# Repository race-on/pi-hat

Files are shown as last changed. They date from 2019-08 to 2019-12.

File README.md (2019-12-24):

Race On Pi HAT
=====

A Raspberry Pi HAT to control a self-driving car. HAT includes:
1. 3.5A DC-DC converter to power the Pi from a battery (2-3 LiPo cells)
2. 10A H-bridge for DC motor control
3. 3A LDO to power servo at 6V for faster response time
4. Battery alarm when the voltage drops under 6V
5. I2C accelerometer interface
6. Interface for encoders based on the QRE1113 analog line sensor
7. Compatible with Jetson Nano
8. Reverse polarity protection
9. Optimized for Seeed Studio PCBA

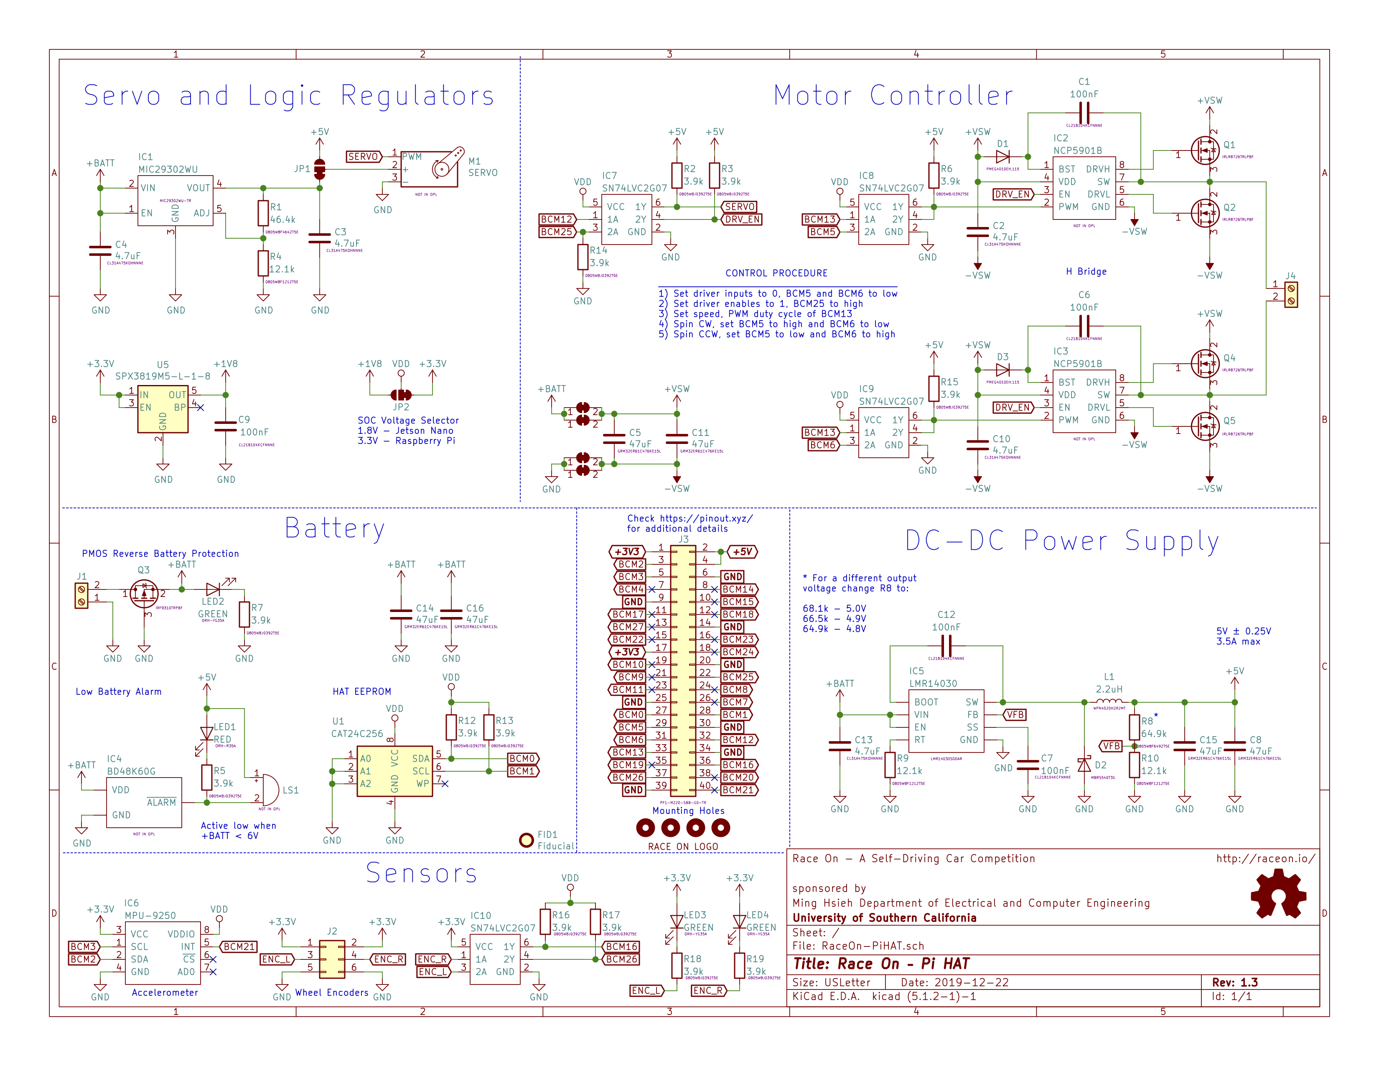
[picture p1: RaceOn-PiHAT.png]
Pi HAT Schematic


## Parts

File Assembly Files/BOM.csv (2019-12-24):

Designator | Manufacturer Part Number or Seeed SKU | Qty
C1, C6, C7, C9, C12 | CL21B104KCFNNNE | 5
C2, C3, C4, C10, C13 | CL31A475KOHNNNE | 5
C5, C8, C11, C14, C15, C16 | CL32A226KAJNNNE | 6
D1, D3 | PMEG4010EH,115 | 2
D2 | MBRS540T3G | 1
IC1 | SPX29302T5-L/TR | 1
IC5 | LMR14030SDDAR | 1
IC7, IC8, IC9, IC10 | SN74LVC2G07DBVR | 4
J2 | A2541WV-2x3P | 1
J3 | PF1-M220-SBB-G0-TR | 1
J1, J4 | 1935161 | 2
L1 | WPN4020H2R2MT | 1
LED1 | ORH-R35A | 1
LED2, LED3, LED4 | ORH-YG35A | 3
M1 | A2543WV-3P | 1
Q3 | IRF9310TRPBF | 1
Q1, Q2, Q4, Q5 | IRLR8726TRLPBF | 4
R1 | 0805W8F4642T5E | 1
R2, R3, R5, R6, R7, R12, R13, R14, R15, R16, R17, R18, R19 | 0805W8J0392T5E | 13
R8 | 0805W8F6492T5E | 1
R4, R9, R10 | 0805W8F1212T5E | 3
U1 | CAT24C256WI-GT3 | 1
U5 | SPX3819M5-L-1-8/TR | 1

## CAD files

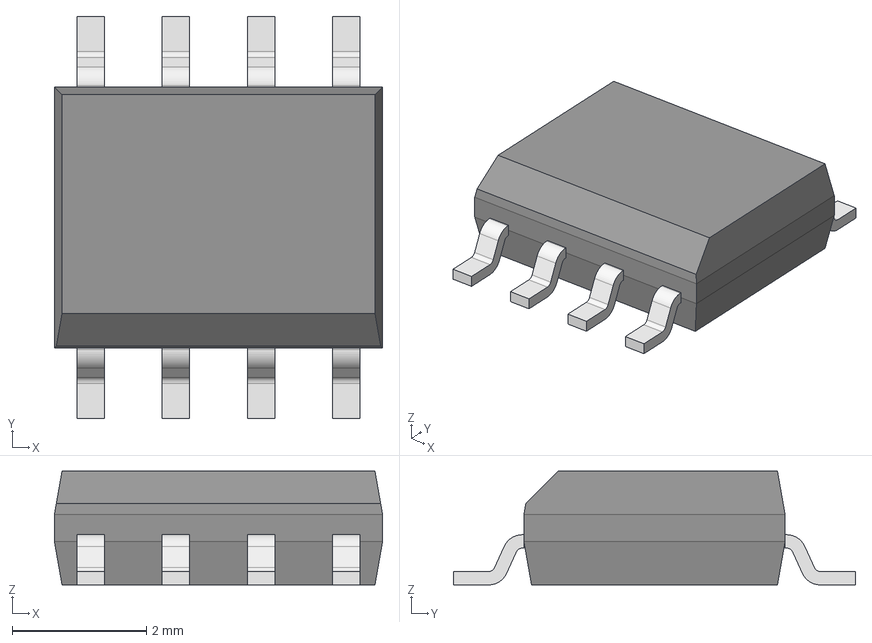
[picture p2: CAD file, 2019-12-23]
3D Models/SOIC9P127_490X600X170L83X41T287X202.STEP
4.90 x 6.00 x 1.70 mm

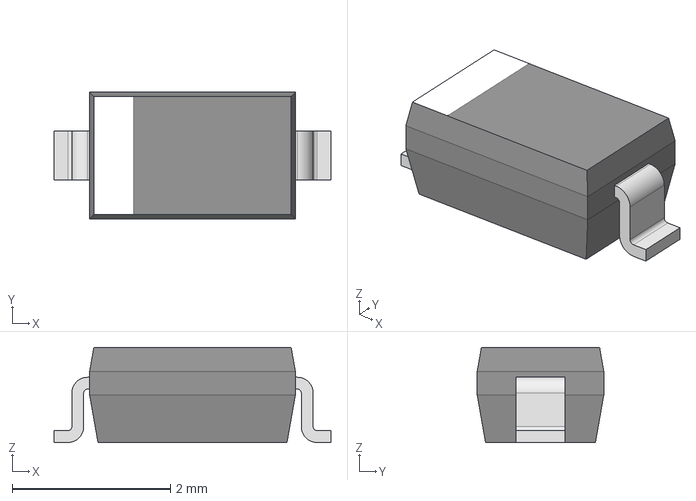
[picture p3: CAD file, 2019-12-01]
3D Models/SOD350X160X120L45X62.STEP
3.50 x 1.60 x 1.20 mm

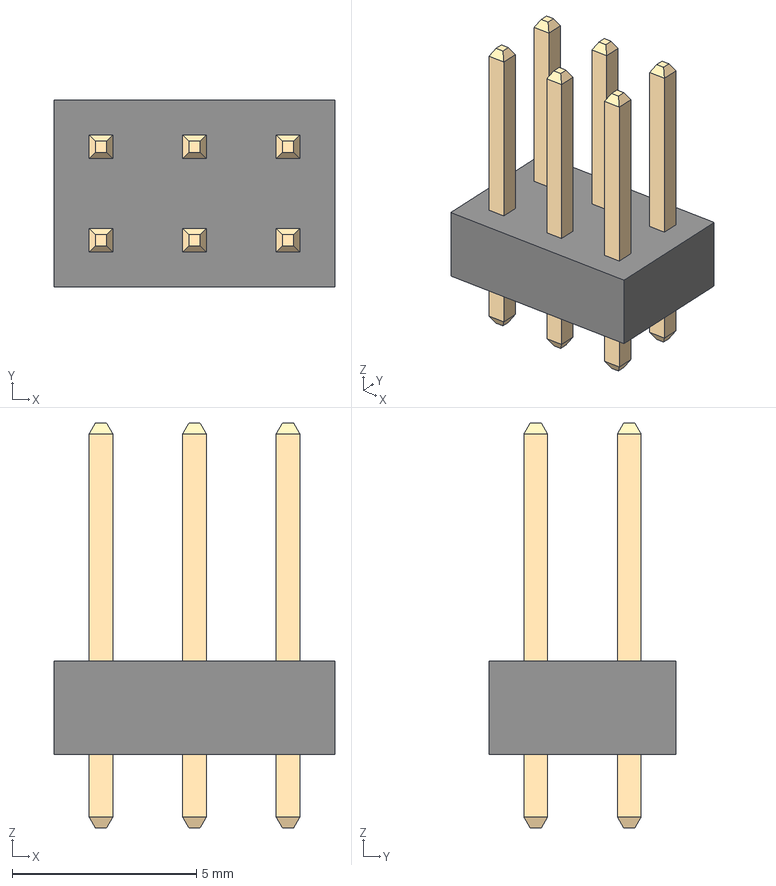
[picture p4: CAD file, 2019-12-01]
3D Models/HDRV6W65P254_3X2_762X508H900.STEP
7.62 x 5.08 x 11.0 mm

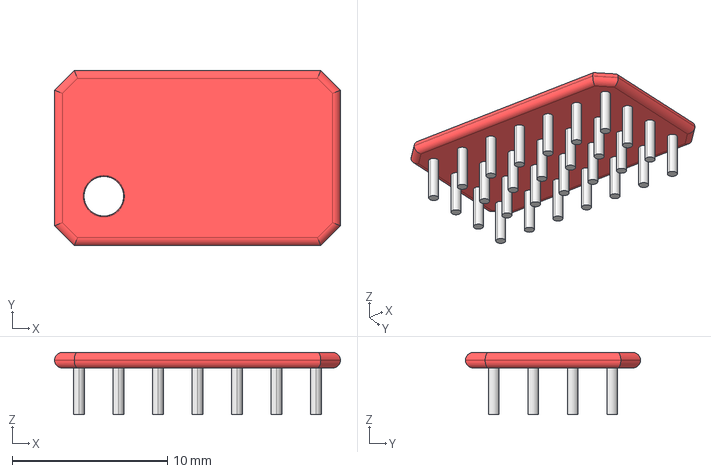
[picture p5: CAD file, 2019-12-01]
3D Models/PGA28P254C7R4L1840X1127H200.STEP
18.4 x 11.3 x 4.00 mm

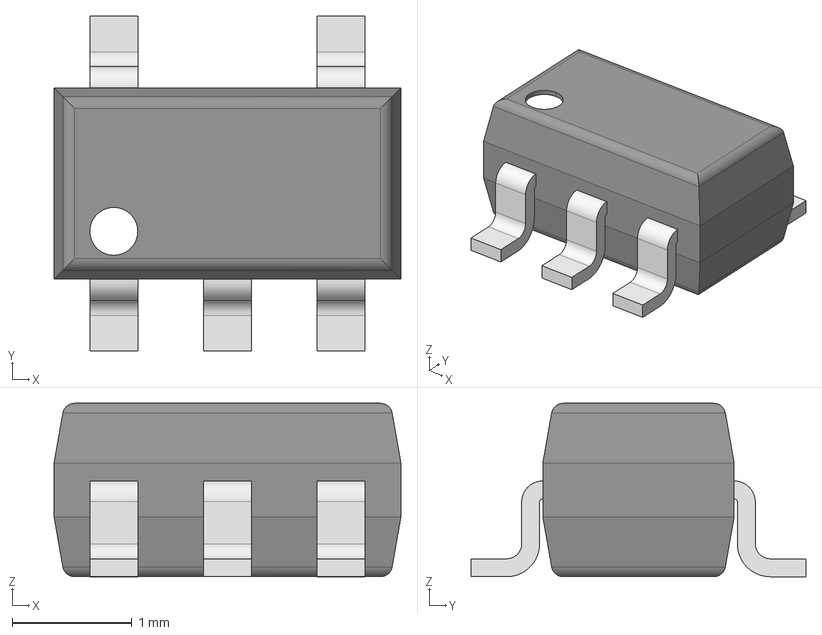
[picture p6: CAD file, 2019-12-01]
3D Models/SOT23-5P95_280X145L45X40.STEP
2.90 x 2.80 x 1.45 mm

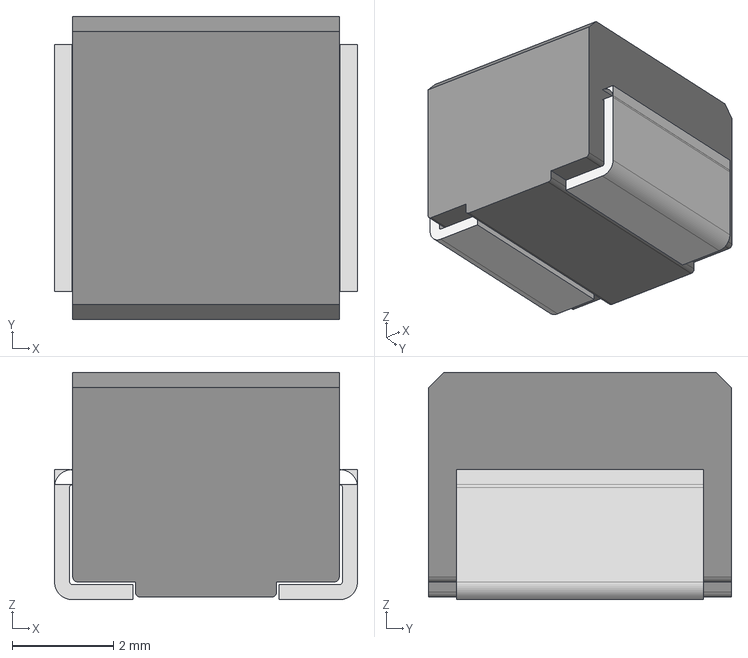
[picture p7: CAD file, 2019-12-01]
3D Models/INDM600X600X450L155X490.STEP
6.00 x 6.00 x 4.50 mm

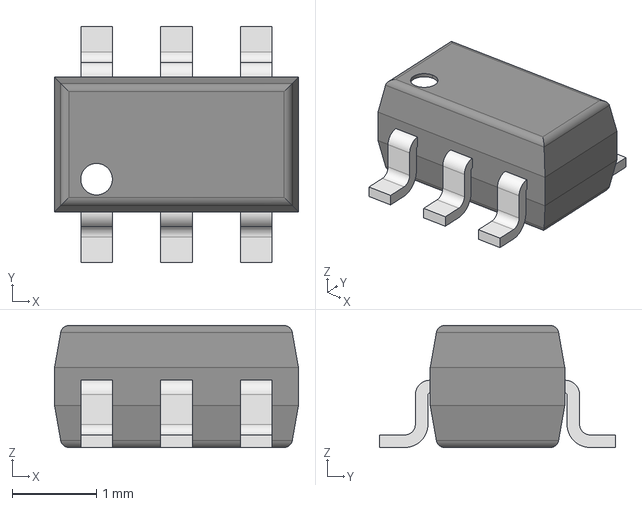
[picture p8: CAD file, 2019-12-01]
3D Models/SOT23-6P95_280X145L45X37.STEP
2.90 x 2.80 x 1.45 mm

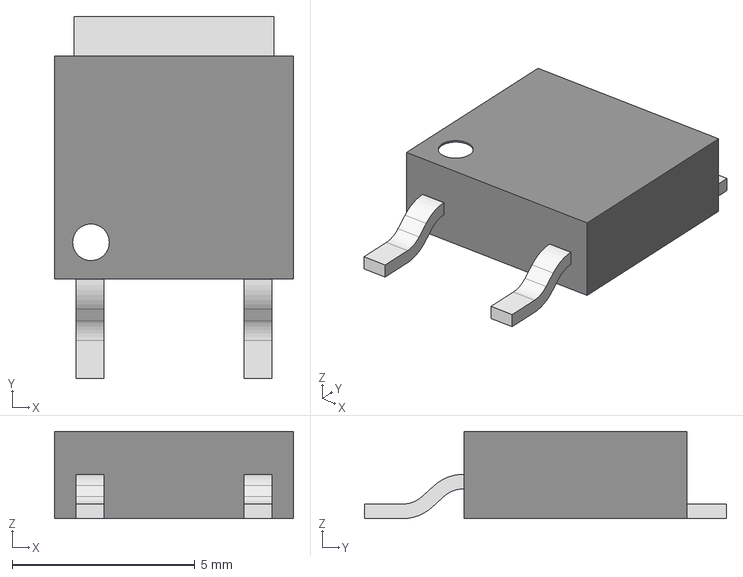
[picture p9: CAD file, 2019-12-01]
3D Models/DPAK3P460_990X239L160X76T650X546.STEP
6.54 x 9.90 x 2.39 mm

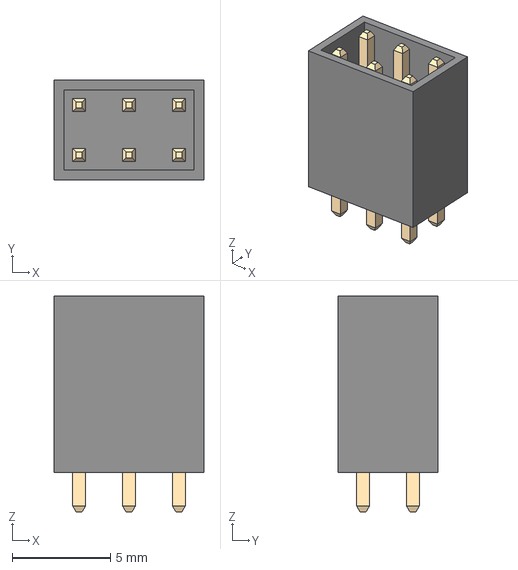
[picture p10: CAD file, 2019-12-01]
3D Models/SHDRV6W65P254_3X2_762X508H900.STEP
7.62 x 5.08 x 11.0 mm

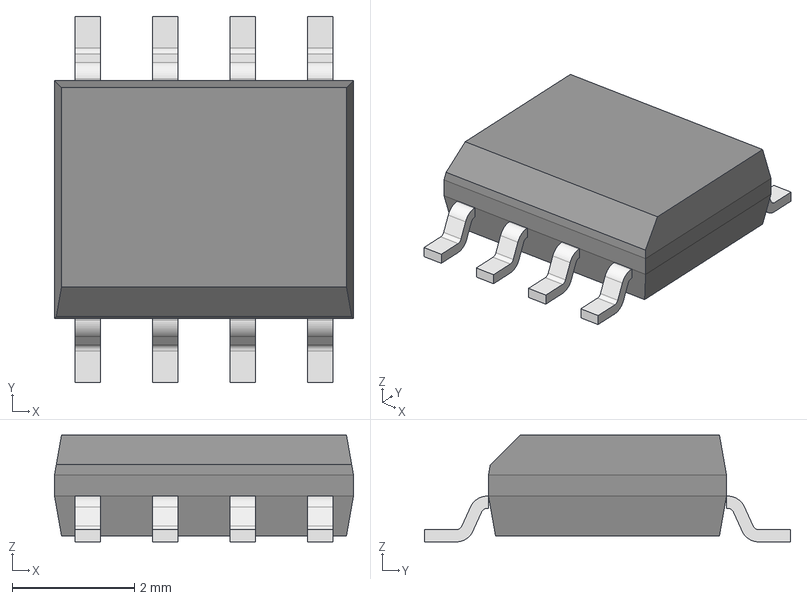
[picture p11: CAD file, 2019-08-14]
3D Models/SOIC8P127_490X600X175L83X42.STEP
4.90 x 6.00 x 1.75 mm

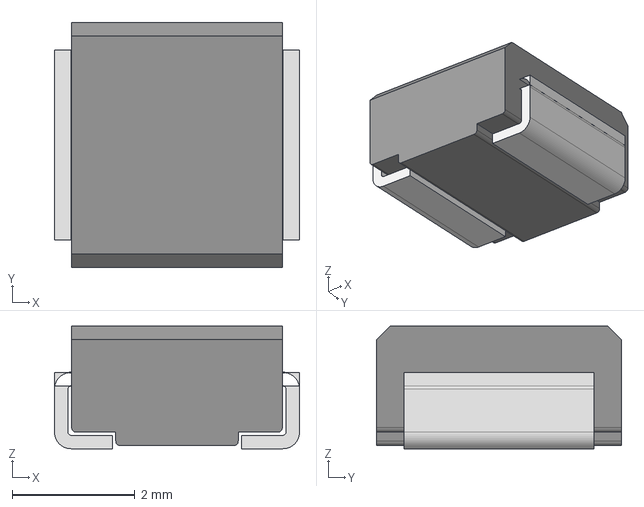
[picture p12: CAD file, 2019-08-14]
3D Models/INDM400X400X200L95X310.STEP
4.00 x 4.00 x 2.00 mm

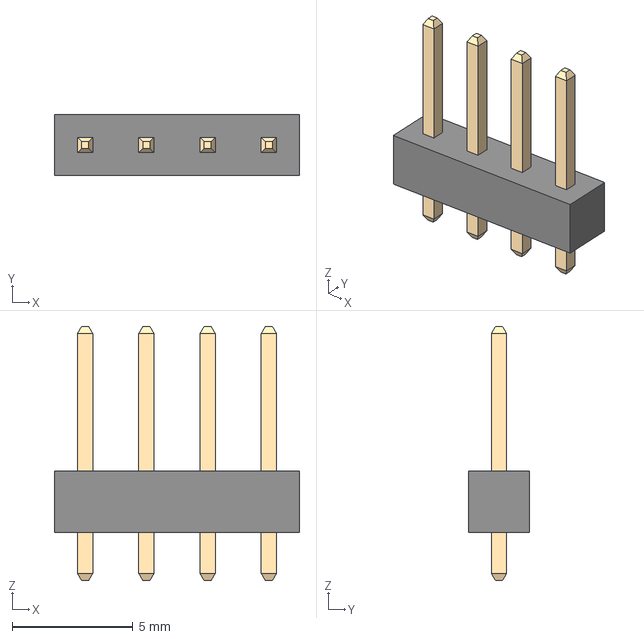
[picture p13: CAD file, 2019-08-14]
3D Models/HDRV4W64P254_4X1_1016X254H854.STEP
10.2 x 2.54 x 10.5 mm

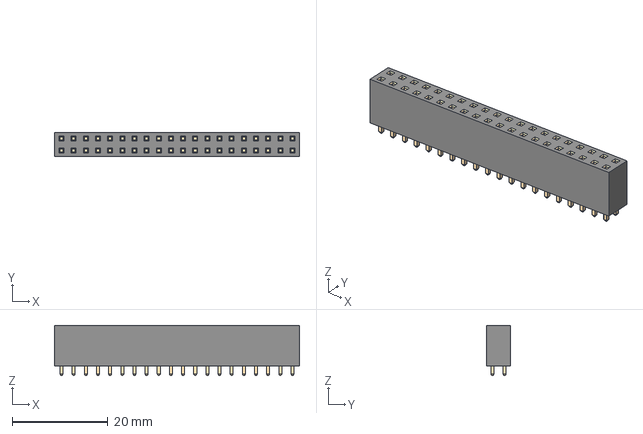
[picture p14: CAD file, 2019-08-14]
3D Models/RHDRV40W64P254_20X2_5120X500H850.STEP
51.2 x 5.00 x 10.5 mm

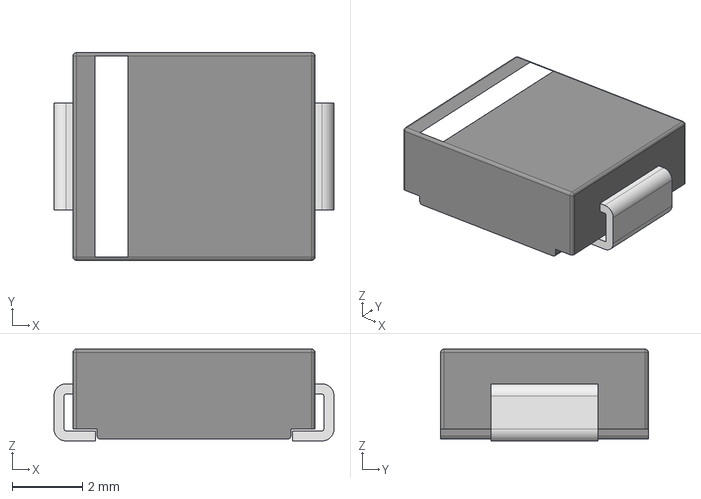
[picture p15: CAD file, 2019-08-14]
3D Models/DIOM795X590X261L117X305.STEP
7.95 x 5.90 x 2.61 mm

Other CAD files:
3D Models/CAPPM730X435X310L135X240.STEP
3D Models/CAPC320X160X180L50.STEP
3D Models/ICSOFL8P127_515X615X112L61X42.STEP
3D Models/CAPC320X250X270L60.STEP
3D Models/BTN4P450_600X900X350L83X70M.STEP
3D Models/CAPC200X125X95L45.STEP
3D Models/DPAK6P67_587X190L89X29T300X275.STEP
3D Models/HDRV3W64P254_3X1_762X254H854.STEP
3D Models/LEDC197X125X85L45.STEP
3D Models/LSP500W60D980H500.STEP
3D Models/RESC200X127X65L40.STEP
3D Models/SOT23-3P95_280X125L45X40.STEP

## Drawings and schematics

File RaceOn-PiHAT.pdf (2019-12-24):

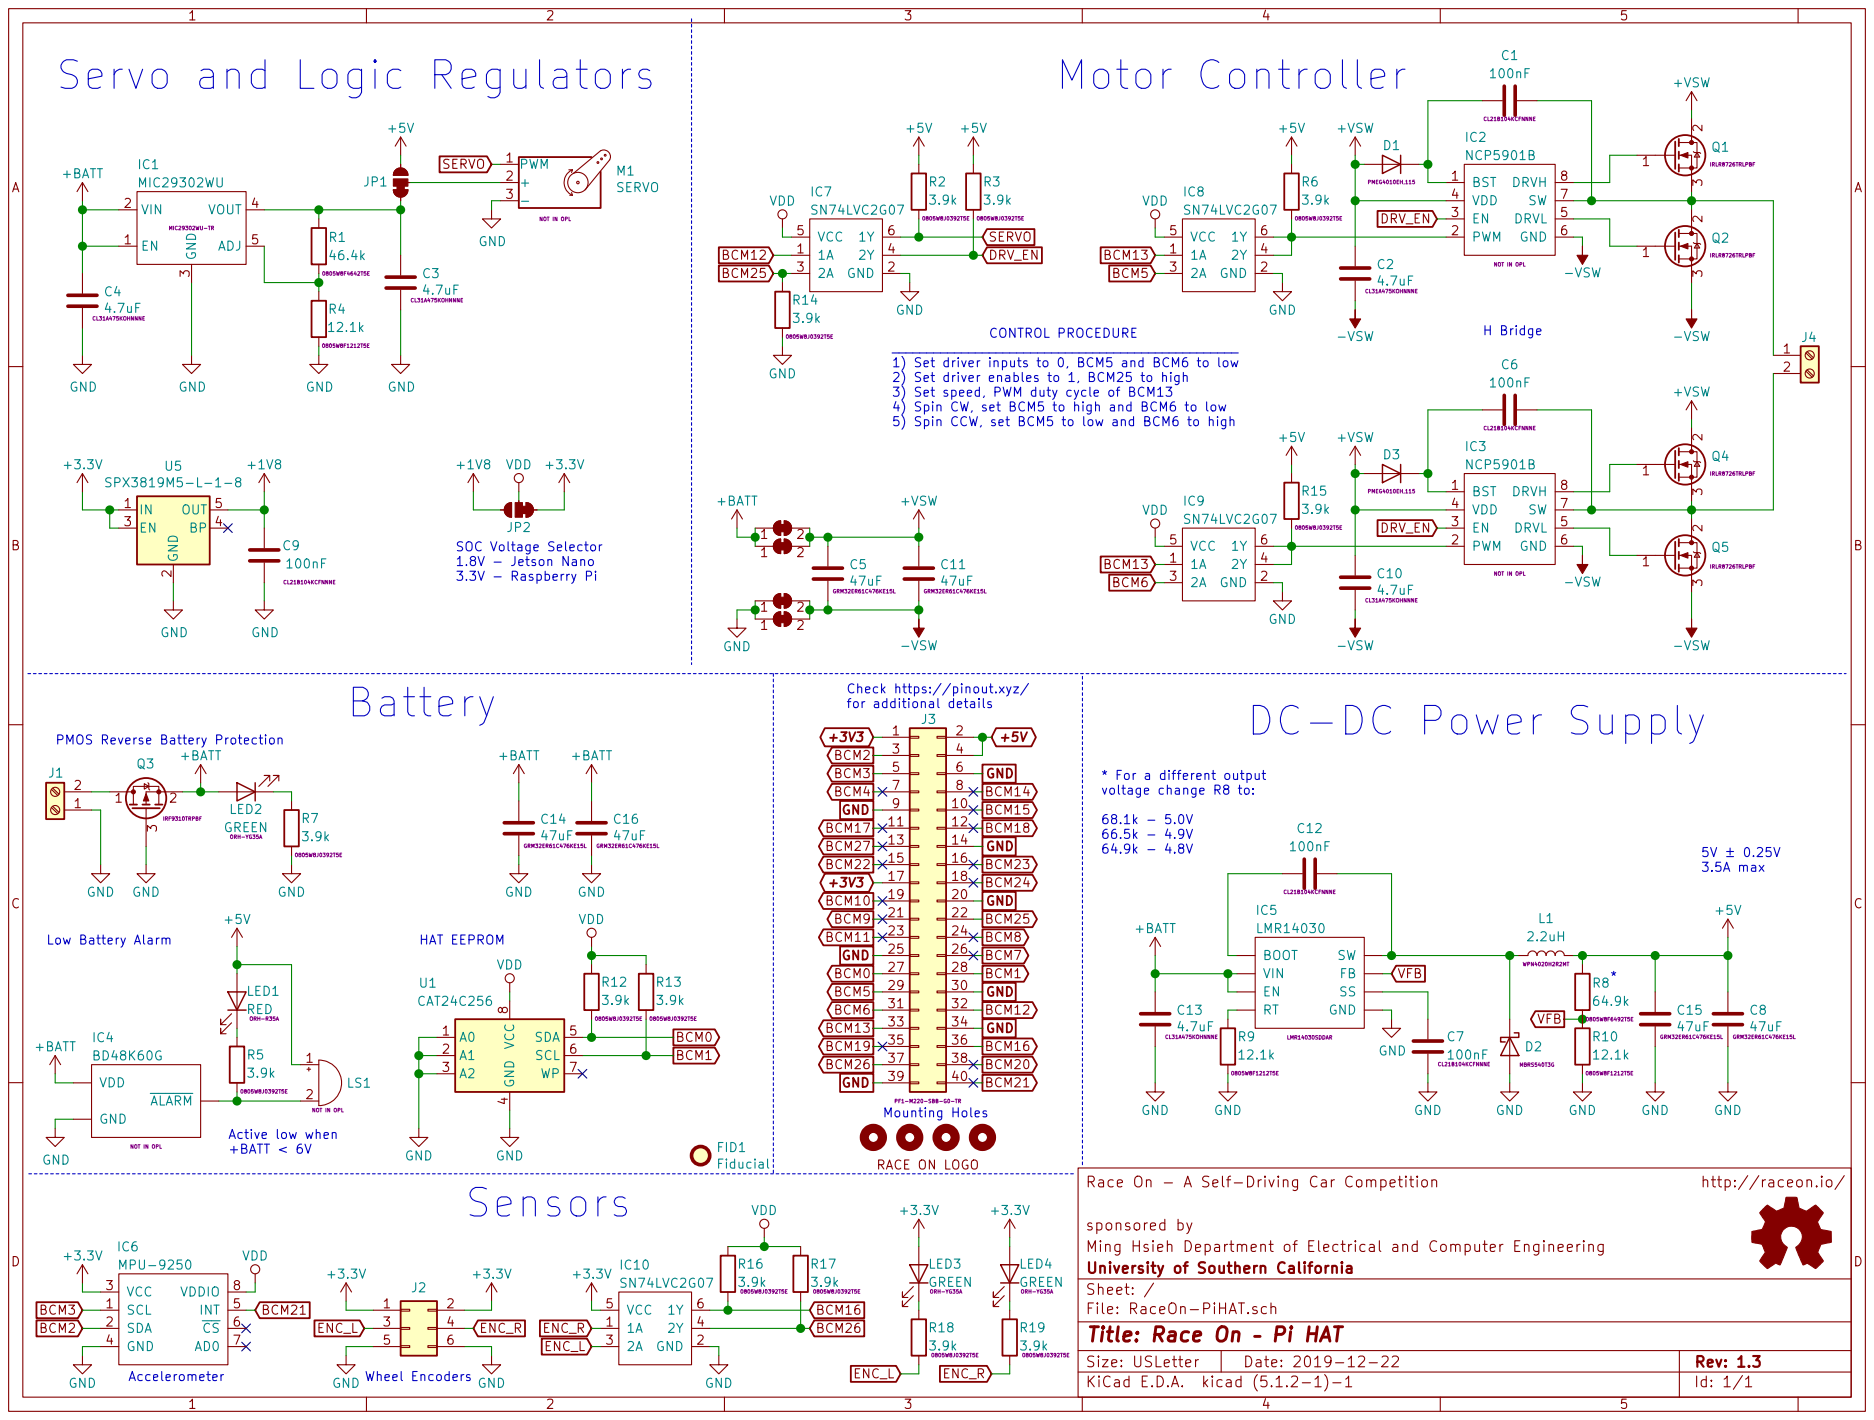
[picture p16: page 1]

+5V Servo and Logic Regulators

1) Set driver inputs to 0, BCM5 and BCM6 to low
2) Set driver enables to 1, BCM25 to high
3) Set speed, PWM duty cycle of BCM13
4) Spin CW, set BCM5 to high and BCM6 to low
5) Spin CCW, set BCM5 to low and BCM6 to high

SOC Voltage Selector 1.8V - Jetson Nano

+3V3 Check https://pinout.xyz/

VFB DC-DC Power Supply

4 SDA 5 SCL 6 WP 7 VCC

Active low when +BATT < 6V

sponsored by
Ming Hsieh Department of Electrical and Computer Engineering
File: RaceOn-PiHAT.sch Sheet: / University of Southern California

Id: 1/1 Title: Race On Pi HAT

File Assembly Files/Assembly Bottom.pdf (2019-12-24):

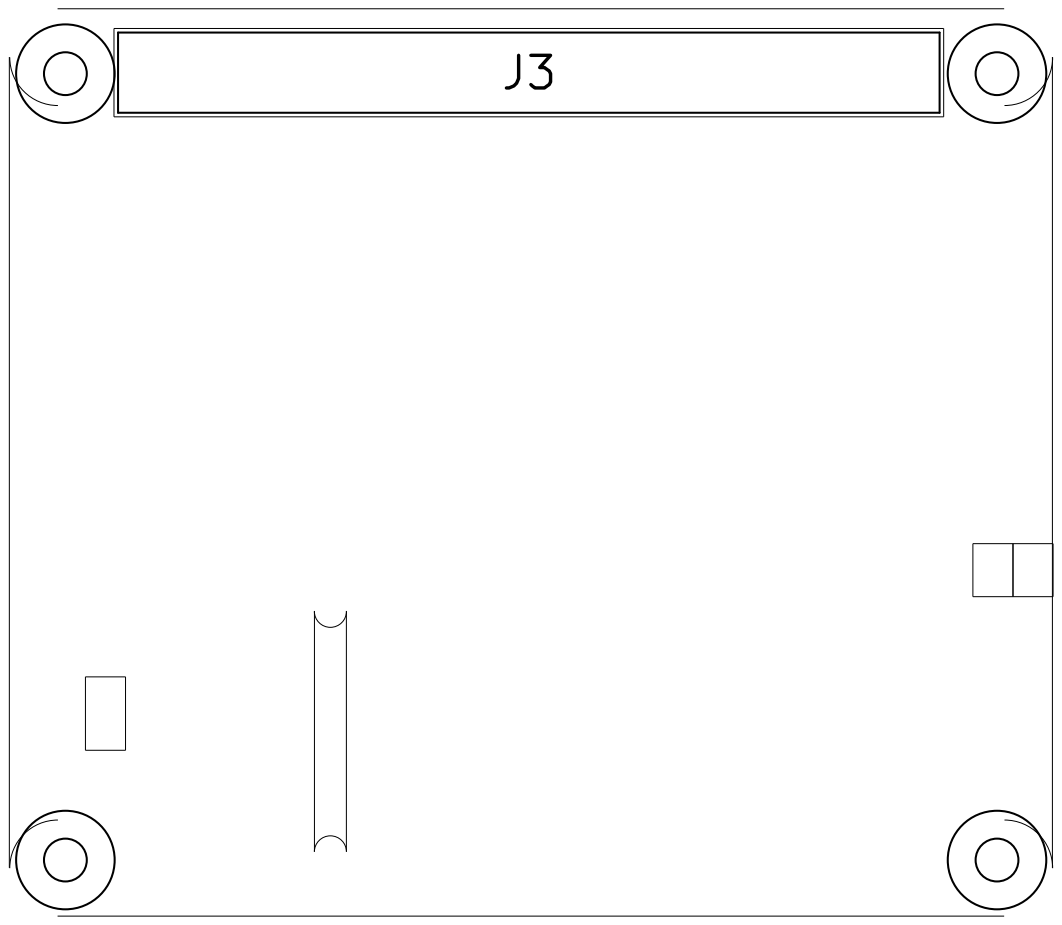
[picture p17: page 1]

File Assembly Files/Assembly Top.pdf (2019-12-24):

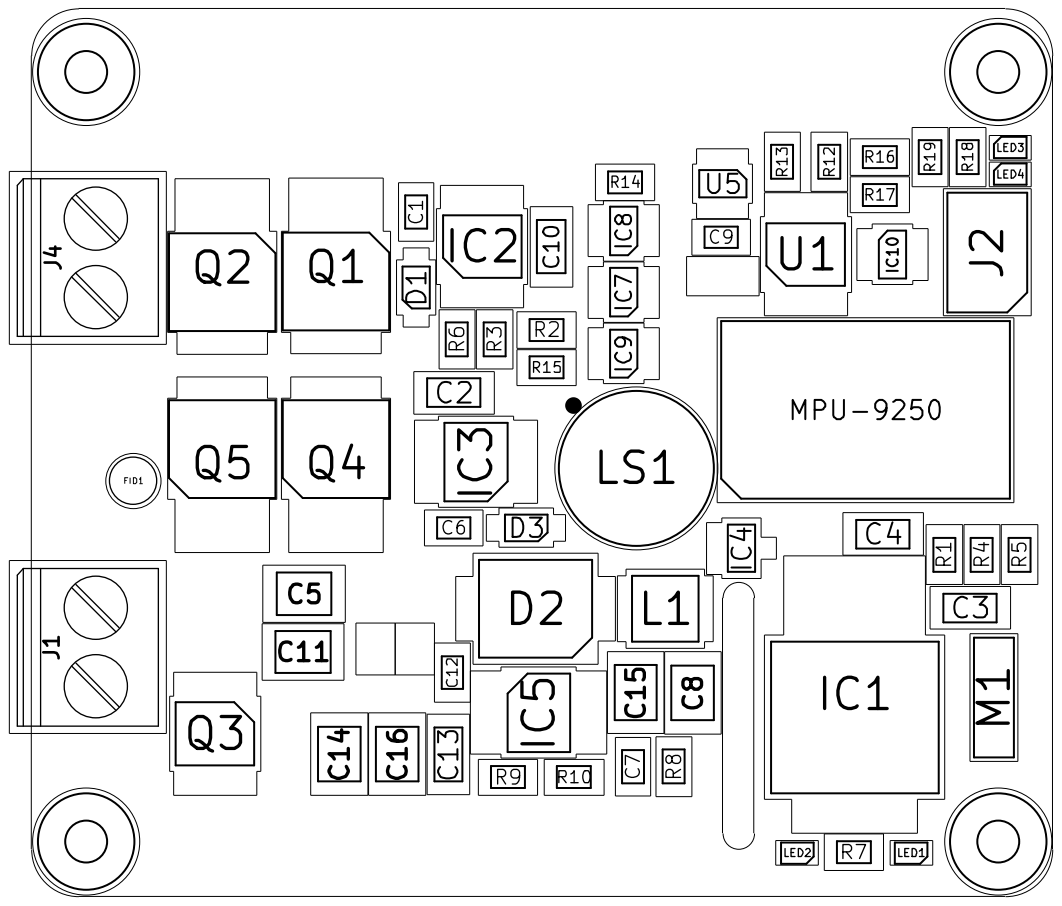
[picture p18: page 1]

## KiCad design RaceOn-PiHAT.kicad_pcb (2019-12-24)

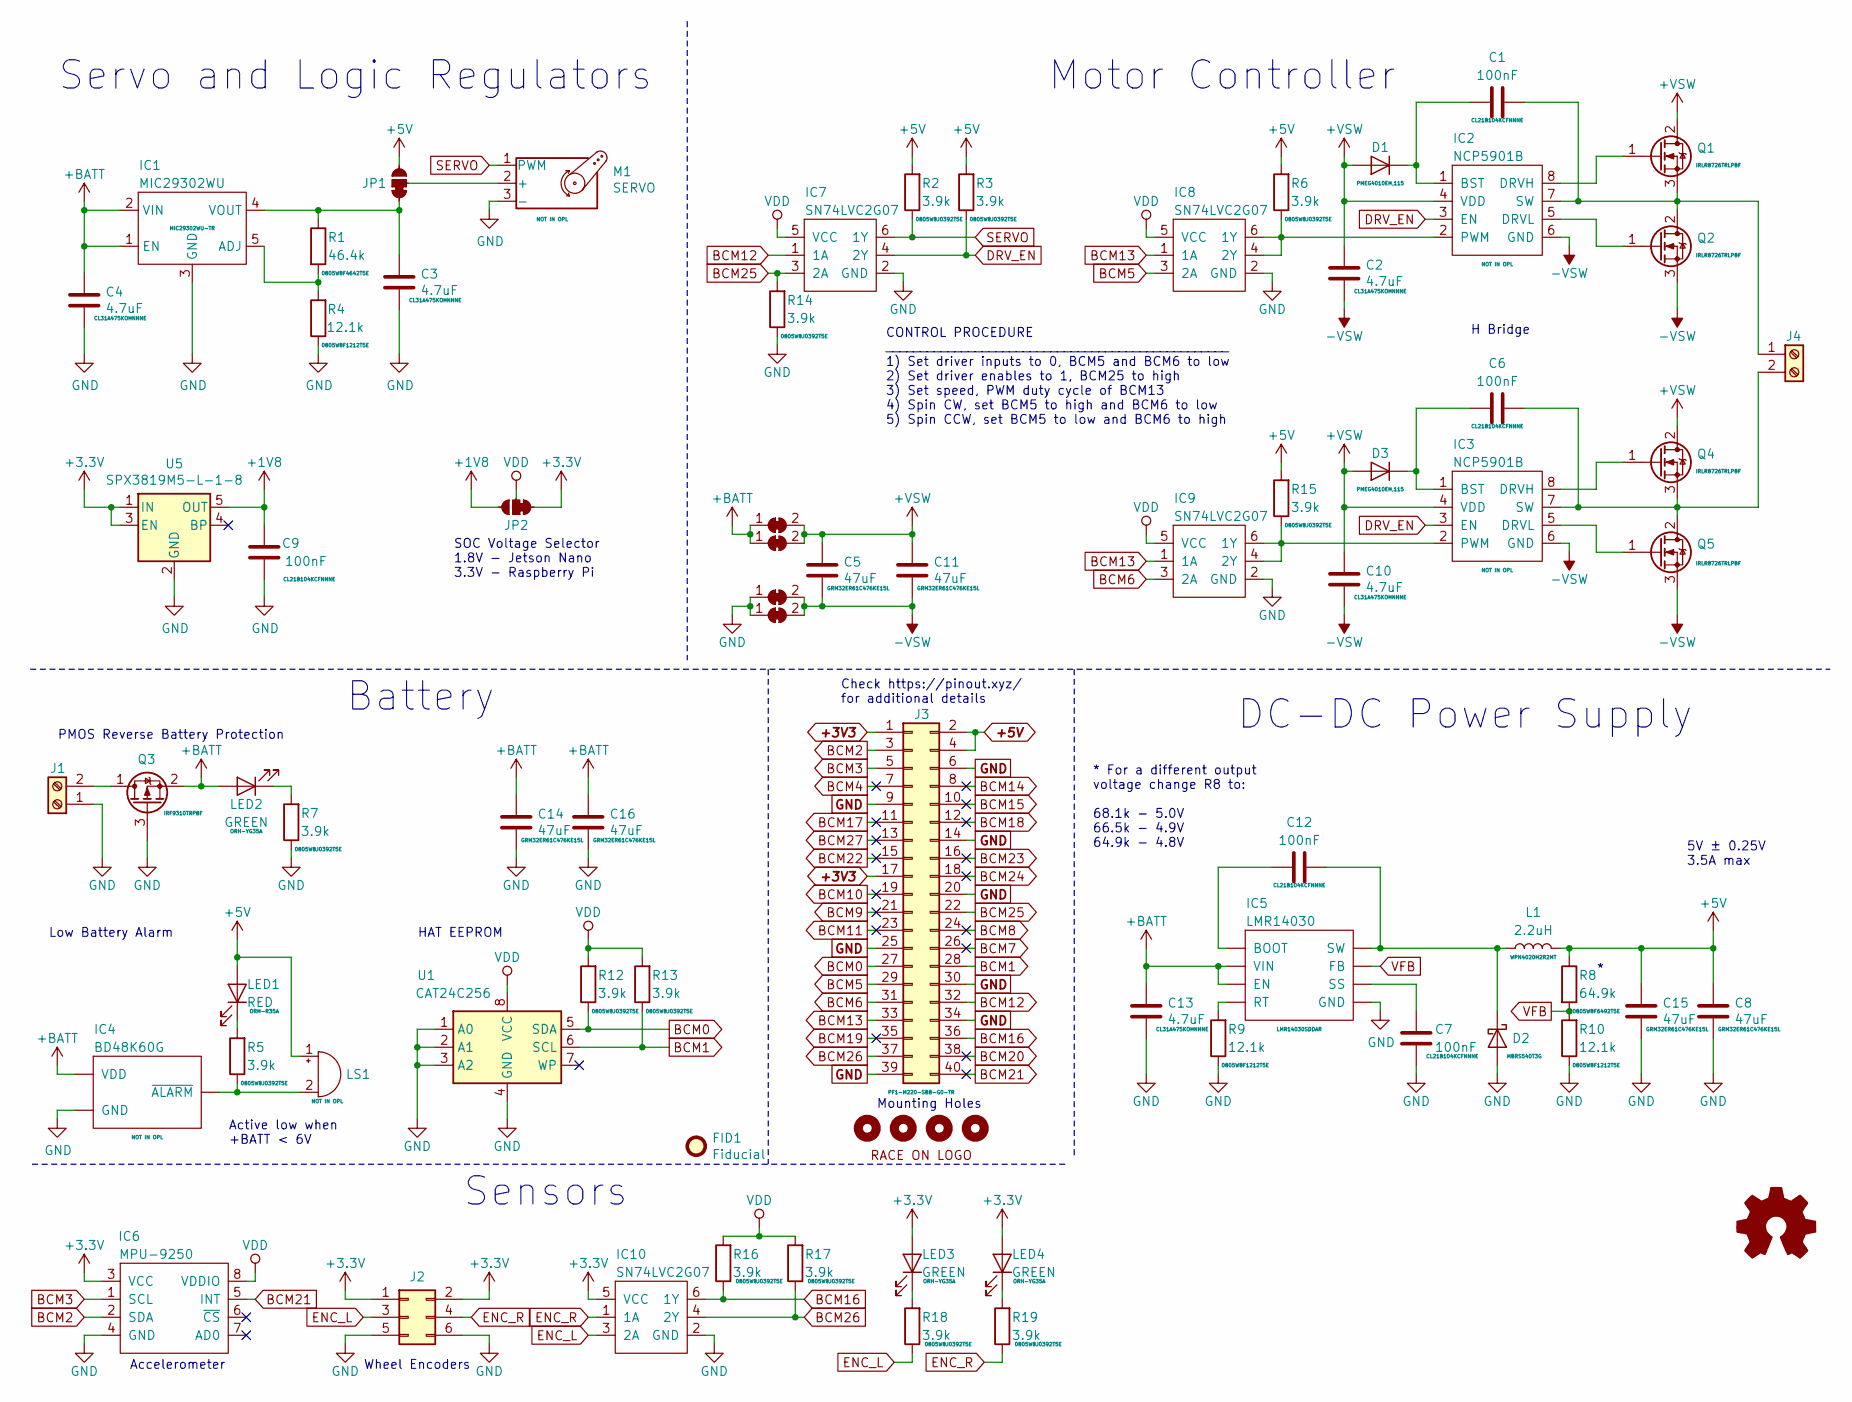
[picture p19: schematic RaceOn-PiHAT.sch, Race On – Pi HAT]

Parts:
C1, C6, C7, C9, C12: 100nF; CAPC200X125X95L45M; MPN CL21B104KCFNNNE
C2, C3, C4, C10, C13: 4.7uF; CAPC320X160X180L50M; MPN CL31A475KOHNNNE
C5, C8, C11, C14, C15, C16: 47uF; CAPC320X250X270L60M; MPN GRM32ER61C476KE15L
D1, D3: D; SOD350X160X120L45X62M; MPN PMEG4010EH,115
D2: D_Schottky; DIOM795X590X261L117X305M; MPN MBRS540T3G
FID1: Fiducial; FID1M3
H1, H2, H3, H4: MountingHole; MTGP620H275V8H50
IC1: MIC29302WU; DPAK6P67_587X190L89X29T300X275M; MPN MIC29302WU-TR
IC2, IC3: NCP5901B; SOIC8P127_490X600X175L83X42M; MPN NOT IN OPL
IC4: BD48K60G; SOT23-3P95_280X125L45X40M; MPN NOT IN OPL
IC5: LMR14030; SOIC9P127_490X600X170L83X41T287X202; MPN LMR14030SDDAR
IC6: MPU-9250; PGA28P254C7R4L1840X1127H200
IC7, IC8, IC9, IC10: SN74LVC2G07; SOT23-6P95_280X145L45X37M; MPN SN74LVC2G07DBVR
J1, J4: Screw_Terminal_01x02; TerminalBlock_Phoenix_PT-1,5-2-5.0-H_1x02_P5.00mm_Horizontal; MPN 1935161
J2: Conn_02x03_Odd_Even; HDRV6W65P254_3X2_762X508H900; MPN A2541WV-2x3P
J3: Pi Connector; RHDRV40W64P254_20X2_5120X500H850; MPN PF1-M220-SBB-G0-TR
JP1, JP2: SolderJumper; SJ3B12P10X15
JP3, JP4, JP5, JP6: SolderJumper_2_Bridged; SolderJumper-2_P1.3mm_Bridged_Pad1.0x1.5mm
L1: 2.2uH; INDM400X400X200L95X310M; MPN WPN4020H2R2MT
LED1: RED; LEDC197X125X85L45L; MPN ORH-R35A
LED2, LED3, LED4: GREEN; LEDC197X125X85L45L; MPN ORH-YG35A
LOGO1: RACEON-LOGO; RACEON
LOGO2: Logo_Open_Hardware_Small; OSHW-Logo2_7.3x6mm_SilkScreen
LS1: AI1027TWT5V2R; LSP500W60D980H500; MPN NOT IN OPL
M1: SERVO; HDRV3W64P254_3X1_762X254H854; MPN NOT IN OPL
Q1, Q2, Q4, Q5: IPD50R380CE; DPAK3P460_990X239L160X76T650X546L; MPN IRLR8726TRLPBF
Q3: SQJA37EP1; SOIC8P127_490X600X175L83X42M-TRANZISTOR; MPN IRF9310TRPBF
R1: 46.4k; RESC200X127X65L40M; MPN 0805W8F4642T5E
R2, R3, R5, R6, R7, R12, R13, R14, R15, R16, R17, R18, R19: 3.9k; RESC200X127X65L40M; MPN 0805W8J0392T5E
R4, R9, R10: 12.1k; RESC200X127X65L40M; MPN 0805W8F1212T5E
R8: 64.9k; RESC200X127X65L40M; MPN 0805W8F6492T5E
U1: CAT24C256; SOIC8P127_490X600X175L83X42M; MPN CAT24C256WI-GT3
U5: SPX3819M5-L-1-8; SOT23-5P95_280X145L45X40M; MPN SPX3819M5-L-1-8/TR

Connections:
+1V8: C9.2, JP2.3 (B), U5.5 (OUT)
+5V: C8.2, C15.2, J3.2, J3.4, JP1.3 (B), L1.1, LED1.2 (A), LS1.1 (-), R2.2, R3.2, R6.2, R8.1, R15.2
+BATT: C4.2, C13.2, C14.2, C16.2, IC1.1 (EN), IC1.2 (VIN), IC4.3 (VDD), IC5.2 (VIN), IC5.3 (EN), JP3.1 (A), JP4.1 (A), LED2.2 (A), Q3.2 (S)
+VSW: C2.2, C5.2, C10.2, C11.2, D1.2 (A), D3.2 (A), IC2.4 (VDD), IC3.4 (VDD), JP3.2 (B), JP4.2 (B), Q1.2 (D), Q4.2 (D)
-VSW: C2.1, C5.1, C10.1, C11.1, IC2.6 (GND), IC3.6 (GND), JP5.2 (B), JP6.2 (B), Q2.3 (S), Q5.3 (S)
BCM0: J3.27, R12.1, U1.5 (SDA)
BCM1: J3.28, R13.1, U1.6 (SCL)
BCM2: IC6.2 (SDA), J3.3
BCM3: IC6.1 (SCL), J3.5
BCM4: J3.7
BCM5: IC8.3 (2A), J3.29
BCM6: IC9.3 (2A), J3.31
BCM7: J3.26
BCM8: J3.24
BCM9: J3.21
BCM10: J3.19
BCM11: J3.23
BCM12: IC7.1 (1A), J3.32
BCM13: IC8.1 (1A), IC9.1 (1A), J3.33
BCM14: J3.8
BCM15: J3.10
BCM16: IC10.6 (1Y), J3.36, R16.1
BCM17: J3.11
BCM18: J3.12
BCM19: J3.35
BCM20: J3.38
BCM21: IC6.5 (INT), J3.40
BCM22: J3.15
BCM23: J3.16
BCM24: J3.18
BCM25: IC7.3 (2A), J3.22, R14.2
BCM26: IC10.4 (2Y), J3.37, R17.1
BCM27: J3.13
DRV_EN: IC2.3 (EN), IC3.3 (EN), IC7.4 (2Y), R3.1
ENC_L: IC10.3 (2A), J2.3, R18.1
ENC_R: IC10.1 (1A), J2.4, R19.1
GND: C3.1, C4.1, C7.1, C8.1, C9.1, C13.1, C14.1, C15.1, C16.1, D2.2 (A), IC1.3 (GND), IC1.6 (GND), IC4.1 (GND), IC5.7 (GND), IC5.9 (GND), IC6.4 (GND), IC7.2 (GND), IC8.2 (GND), IC9.2 (GND), IC10.2 (GND), J1.1, J2.5, J2.6, J3.6, J3.9, J3.14, J3.20, J3.25, J3.30, J3.34, J3.39, JP5.1 (A), JP6.1 (A), M1.3 (-), Q3.3 (G), R4.1, R7.1, R9.1, R10.1, R14.1, U1.1 (A0), U1.2 (A1), U1.3 (A2), U1.4 (GND), U5.2 (GND)
unnamed: C1.1, IC2.7 (SW), J4.1, Q1.3 (S), Q2.2 (D)
unnamed: C1.2, D1.1 (K), IC2.1 (BST)
unnamed: C3.2, IC1.4 (VOUT), JP1.1 (A), R1.1
unnamed: C6.1, IC3.7 (SW), J4.2, Q4.3 (S), Q5.2 (D)
unnamed: C6.2, D3.1 (K), IC3.1 (BST)
unnamed: C7.2, IC5.6 (SS)
unnamed: C12.1, D2.1 (K), IC5.8 (SW), L1.2
unnamed: C12.2, IC5.1 (BOOT)
unnamed: IC1.5 (ADJ), R1.2, R4.2
unnamed: IC2.2 (PWM), IC8.4 (2Y), IC8.6 (1Y), R6.1
unnamed: IC2.5 (DRVL), Q2.1 (G)
unnamed: IC2.8 (DRVH), Q1.1 (G)
unnamed: IC3.2 (PWM), IC9.4 (2Y), IC9.6 (1Y), R15.1
unnamed: IC3.5 (DRVL), Q5.1 (G)
unnamed: IC3.8 (DRVH), Q4.1 (G)
unnamed: IC4.2 (~ALARM), LS1.2 (+), R5.1
unnamed: IC5.4 (RT), R9.2
unnamed: J1.2, Q3.1 (D)
unnamed: JP1.2 (C), M1.2 (+)
unnamed: LED1.1 (K), R5.2
unnamed: LED2.1 (K), R7.2
unnamed: LED3.1 (K), R18.2
unnamed: LED4.1 (K), R19.2
SERVO: IC7.6 (1Y), M1.1 (PWM), R2.1
VDD: IC6.8 (VDDIO), IC7.5 (VCC), IC8.5 (VCC), IC9.5 (VCC), JP2.2 (C), R12.2, R13.2, R16.2, R17.2, U1.8 (VCC)
VFB: IC5.5 (FB), R8.2, R10.2

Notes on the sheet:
DC-DC Power Supply
5V ± 0.25V 3.5A max
Motor Controller
Low Battery Alarm
* For a different output voltage change R8 to: 68.1k - 5.0V 66.5k - 4.9V 64.9k - 4.8V
Servo and Logic Regulators
H Bridge
SOC Voltage Selector 1.8V - Jetson Nano 3.3V - Raspberry Pi
Sensors
Accelerometer
Wheel Encoders
Check https://pinout.xyz/ for additional details
Mounting Holes
PMOS Reverse Battery Protection
HAT EEPROM
CONTROL PROCEDURE __________________________________________________ 1) Set driver inputs to 0, BCM5 and BCM6 to low 2) Set driver enables to 1, BCM25 to high 3) Set speed, PWM duty cycle of BCM13 4) Spin CW, set BCM5 to high and BCM6 to low 5) Spin CCW, set BCM5 to low and BCM6 to high
Battery
Active low when +BATT < 6V

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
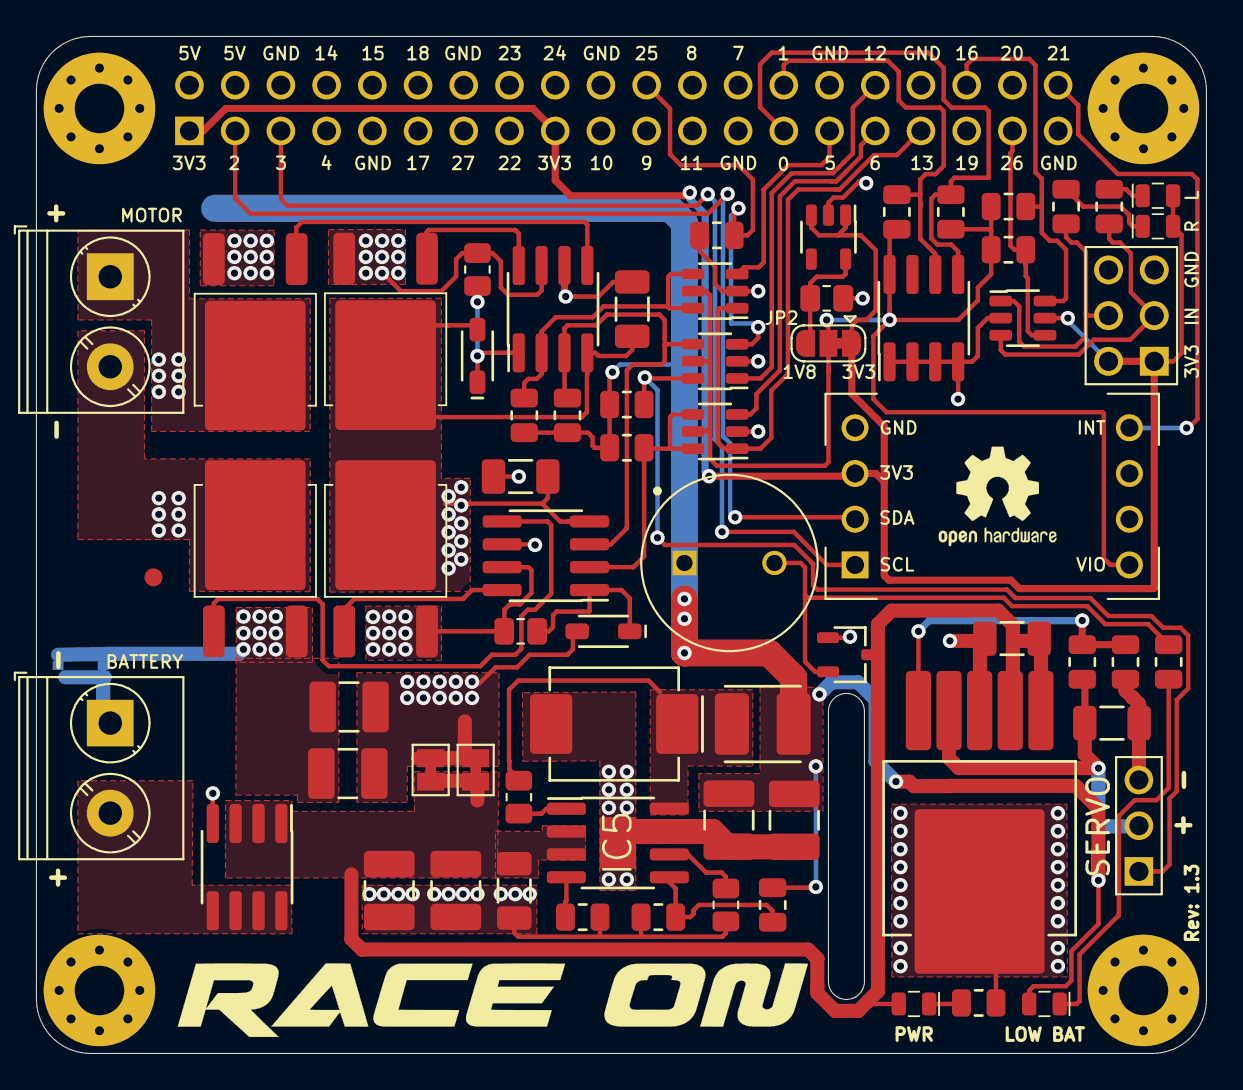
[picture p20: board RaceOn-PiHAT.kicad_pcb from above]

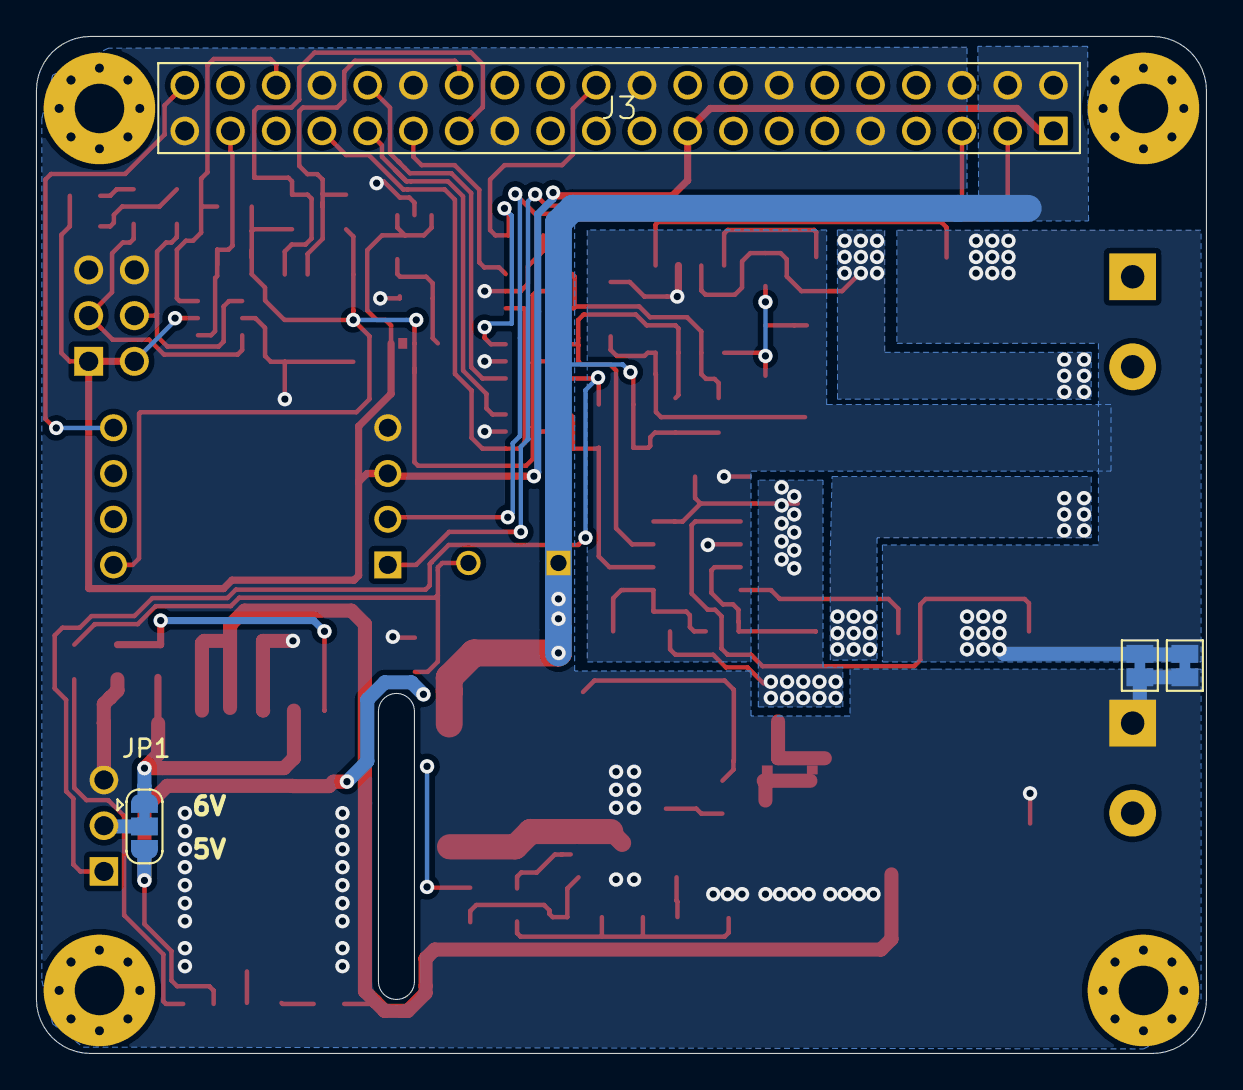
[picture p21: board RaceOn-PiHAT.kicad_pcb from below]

Board: 2 copper layers, 65.0 x 56.5 mm, 78 parts (4 on the bottom side), 48 nets.

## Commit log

2019-07-03 labels added
    [first_design.sch]
2019-07-08 buzzer layout + buttons added
    [first_design.sch]
2019-07-09 IR Circuit added
    [first_design.sch]
2019-07-09 IR circuit fix
    [first_design.sch]
2019-07-10 ldo added
    [first_design.sch]
2019-07-11 footprint-libraries added
    [first_design.sch]
2019-07-11 updating footprints
    [first_design.sch]
2019-07-11 edge cut added
    [first_design.kicad_pcb, first_design.sch]
2019-07-12 footprints added
    [first_design.sch]
2019-07-13 some connectors footprints added
    [first_design.sch]
2019-07-13 raspberry pin headers added for review
    [first_design.sch]
2019-07-13 motor & power connector pending changes
    [first_design.sch]
2019-07-13 working on PCB design
    [first_design.kicad_pcb, first_design.sch]
2019-07-14 PCB Board first layout
    [first_design.kicad_pcb, first_design.sch]
2019-07-14 PCB board in the works
    [first_design.kicad_pcb, first_design.sch]
2019-07-16 playing with PiHat footprint
    [first_design.kicad_pcb]
2019-07-16 fitting components in piHat
    [first_design.kicad_pcb]
2019-07-16 Night Session
    [first_design.kicad_pcb, first_design.sch]
2019-07-18 traced buck
    [first_design.kicad_pcb, first_design.sch]
2019-07-18 Stuck trying to trace Pi connector pins. Need some tips
    [first_design.kicad_pcb]
2019-07-20 Before changes
    [first_design.kicad_pcb, first_design.sch]
2019-07-22 working on tracing, back layer is messed up
    [first_design.kicad_pcb, first_design.sch]
2019-07-22 Killing it
    [first_design.kicad_pcb, first_design.sch]
2019-07-22 Everything is wired, fixed schematic, haven't found PMOS and IR yet. Check PCB design
    [first_design.kicad_pcb, first_design.sch]
2019-07-23 final touches
    [first_design.kicad_pcb, first_design.sch]
2019-07-23 final final touches
    [first_design.kicad_pcb, first_design.sch]
2019-07-23 schematic edit
    [first_design.sch]
2019-07-23 still finalizing
    [first_design.kicad_pcb, first_design.sch]
2019-07-25 Ready for PCB Prototyping
    [CAPC320X160X180L50.STEP, CAPC320X250X180L50.STEP, DPAK3P457_1010X238L155X81T525X470.STEP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]
2019-08-03 Remove extra components after playing with the first prototype
    [bom.csv, bom2.csv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]
2019-08-09 Before deleting old motor controller
    [SOIC16P127_990X600X175L83X41.STEP, first_design.kicad_pcb, first_design.sch]
2019-08-09 Late night commit for schematic
    [first_design.sch]
2019-08-09 Renamed project to RaceOn-PiHAT
    [RaceOn-PiHAT.kicad_pcb, RaceOn-PiHAT.sch, first_design.sch]
2019-08-09 Renamed the project
    [RaceOn-PiHAT.kicad_pcb, RaceOn-PiHAT.sch]
2019-08-10 Included all parts in the schematic
    [RaceOn-PiHAT.kicad_pcb, RaceOn-PiHAT.sch]
2019-08-12 Assign OPL number to each part to be assembled
    [RaceOn-PiHAT.sch]
2019-08-14 Add footprints for all parts
    [BTN4P450_600X900X350L83X70M.STEP, CAPC200X125X95L45.STEP, CAPC320X160X180L50.STEP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]
2019-08-16 Ordered from Seeed PCBA
    [RaceOn-PiHAT.kicad_pcb, RaceOn-PiHAT.sch]
2019-12-01 Version 2
    [BOM.csv, DPAK3P460_990X239L160X76T650X546.STEP, HDRV6W65P254_3X2_762X508H900.STEP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]
2019-12-20 Latest version
    [BOM-test.csv]
2019-12-22 Partial fix
    [RaceOn-PiHAT.kicad_pcb, RaceOn-PiHAT.sch]
2019-12-22 Reverded to production board
    [RaceOn-PiHAT.kicad_pcb, RaceOn-PiHAT.sch]
2019-12-22 Update .gitignore for KiCAD projects
2019-12-22 Reposition IMU and fix labels
    [RaceOn-PiHAT.kicad_pcb, RaceOn-PiHAT.sch]
2019-12-23 Remove EMI filter, replace low ESR caps with ceramic
    [RaceOn-PiHAT.kicad_pcb, RaceOn-PiHAT.sch]
2019-12-23 Labeled motor and battery connectors
    [RaceOn-PiHAT.kicad_pcb]
2019-12-23 Finished board
    [RaceOn-PiHAT.kicad_pcb, RaceOn-PiHAT.sch, SOIC9P127_490X600X170L83X41T287X202.STEP]
2019-12-23 Add new footprint for the DC-DC IC
2019-12-24 Rev 1.3 final
    [BOM.csv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]
2019-12-24 Clean repo from old files
    [CAPC320X160X180L50.STEP, CAPC320X250X180L50.STEP, DPAK3P457_1010X238L155X81T525X470.STEP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]
2019-12-24 Add schematic image

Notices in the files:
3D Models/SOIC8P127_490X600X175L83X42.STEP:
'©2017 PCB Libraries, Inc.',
